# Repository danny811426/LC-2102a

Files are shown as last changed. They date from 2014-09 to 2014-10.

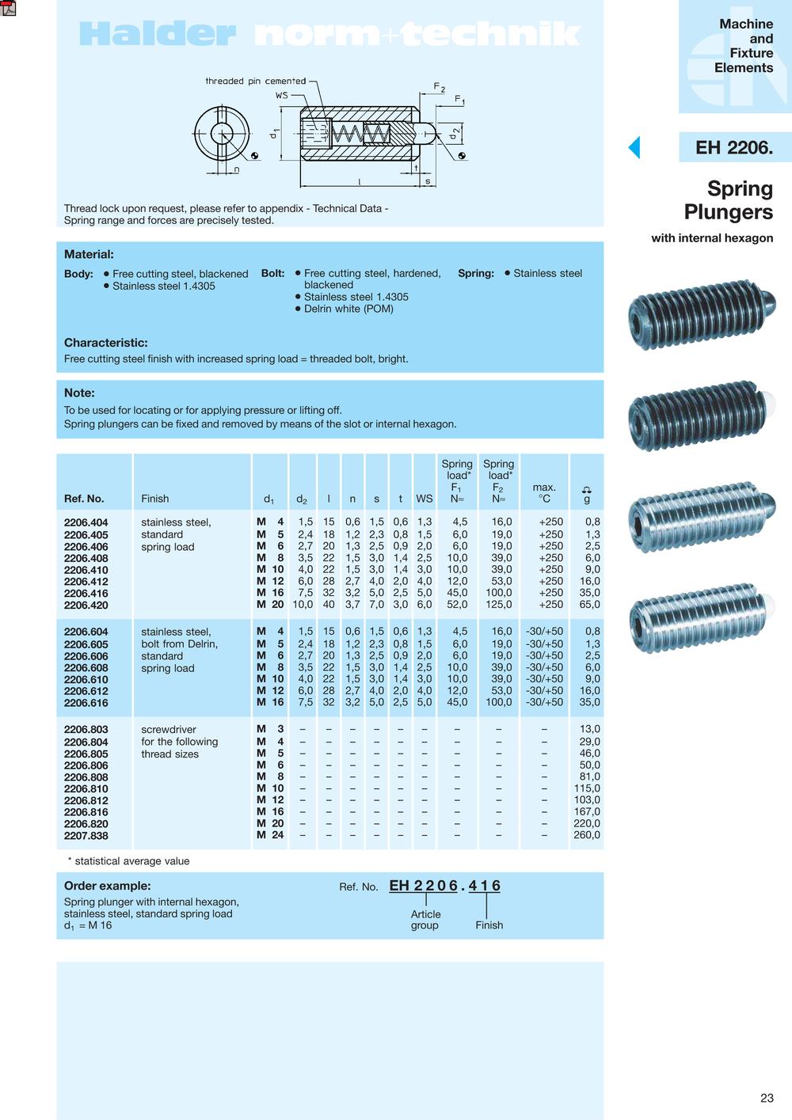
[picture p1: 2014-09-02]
design/datasheets/2206.404 spring plungers.jpg

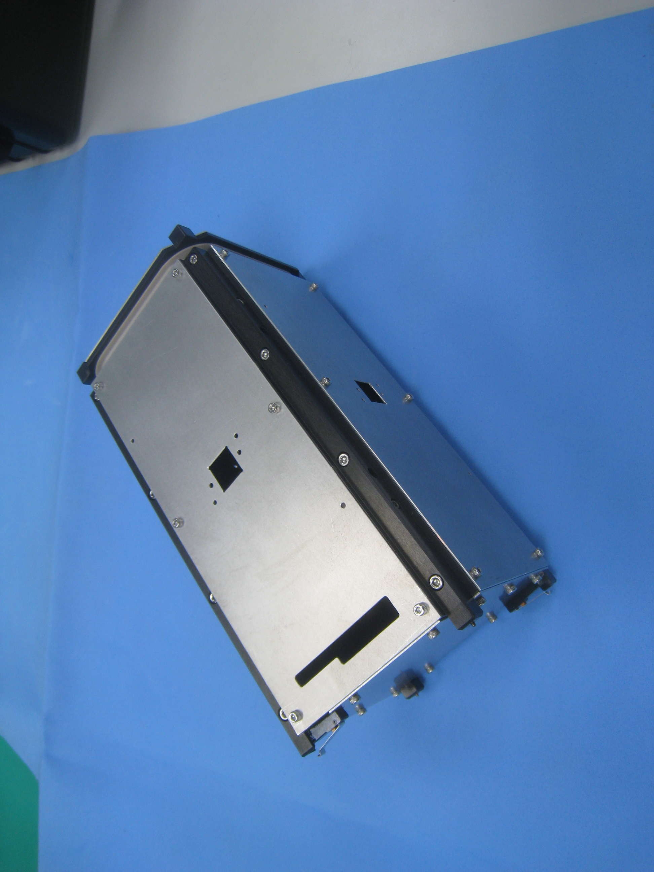
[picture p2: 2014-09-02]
documentation/pictures/IMG_3512.JPG

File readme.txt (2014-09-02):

---------------------------------------
LibreCube LC-2102a 2U CubeSat Structure 
---------------------------------------

OVERVIEW
--------
The LC-2102a 2U CubeSat Structure is a rigid and modular structure for 
nanosatellites that fully conforms to the CubeSat specification. It consists 
of four anodized side frames and a bottom frame, an antenna mounting ring, 
and panels. The frame and panels are made of 6061 aluminium alloy, while the 
antenna mounting ring is made of PEEK. The product fits CubeSat-Kit compatible 
boards and standard PC104 boards.

DISCLAIMER
----------
This product package is distributed in the hope that it will be useful, but 
WITHOUT ANY WARRANTY; without even the implied warranty of MERCHANTABILITY or 
FITNESS FOR A PARTICULAR PURPOSE. See the applicable licenses for more details.

AUTHORS
-------
Release a
* Artur Scholz <artur.scholz@cubesat.de>
* Yannick Lammen

ACKNOWLEDGEMENTS
----------------
The original work (Release a) was carried out at and with support from 
National Cheng Kung University (www.ncku.edu.tw) under supervision of 
Prof. Jiun-Jih Miau and Prof. Jyh-Ching Juang and with the help from students 
of PACELAB and MECLAB of National Cheng Kung University.

RELEASE HISTORY
---------------
Release a
* First release

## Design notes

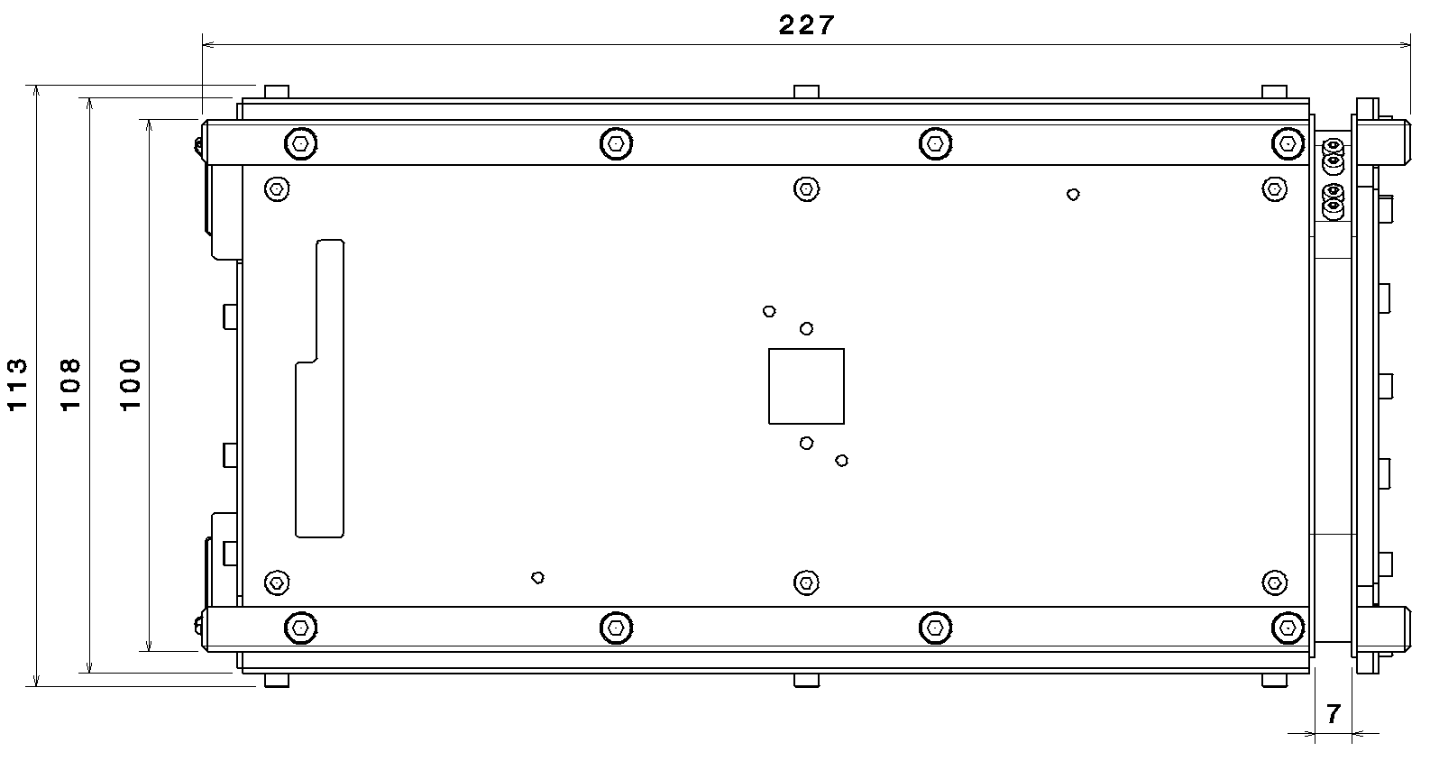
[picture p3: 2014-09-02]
documentation/figures/dimensions.tif

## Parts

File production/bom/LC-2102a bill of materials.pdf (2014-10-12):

Sheet1

Page 1

LC-2102a Bill of Materials

Item | Description | Qty | Part Number / Notes
1 | frame A | 2 | Al-6061, anodized
2 | frame B | 2 | Al-6061, anodized
3 | frame C | 1 | Al-6061, anodized
4 | panel 1 | 1 | Al-6061
5 | panel 2 | 3 | Al-6061
6 | panel 5 | 1 | Al-6061
7 | panel 6 | 1 | Al-6061
8 | board mounting block FLU | 2 | PEEK
9 | board mounting block FRU | 2 | PEEK
10 | board mounting block BRU | 1 | PEEK
11 | board mounting block BLD | 1 | PEEK
12 | board mounting block BLU | 1 | PEEK
13 | board mounting block BRD | 1 | PEEK
14 | antenna ring | 1 | PEEK
15 | M2x10 | 10 | ISO 4762 hexagon socket head cap, aluminum
16 | M2.5x4 | 44 | ISO 4762 hexagon socket head cap, aluminum
17 | M2.5x5 | 16 | ISO 4762 hexagon socket head cap, aluminum
18 | M3x10 | 16 | ISO 4762 hexagon socket head cap, aluminum
19 | M3x16 | 10 | ISO 4762 hexagon socket head cap, aluminum
20 | separation spring | 2 | 15 mm body, 1.5 mm ball and ball height (IMAO: PL4-SUS; KIPP: 03055-04)
21 | deployment switch | 2 | (Digikey: SW247-ND; OMRON: SS-10GL13T)

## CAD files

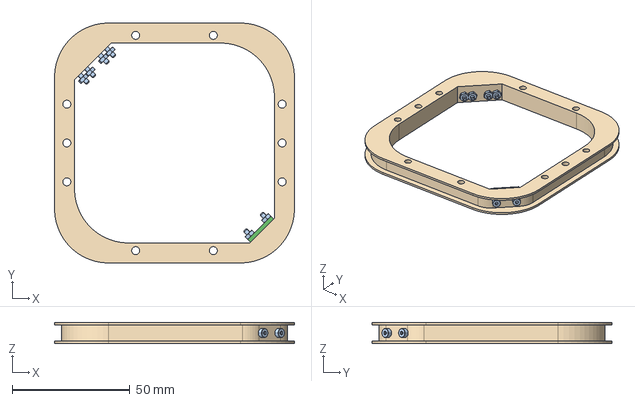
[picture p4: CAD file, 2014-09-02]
production/mechanical/iges/assemblies/antenna ring assembly.igs
102.0 x 102.0 x 9.00 mm

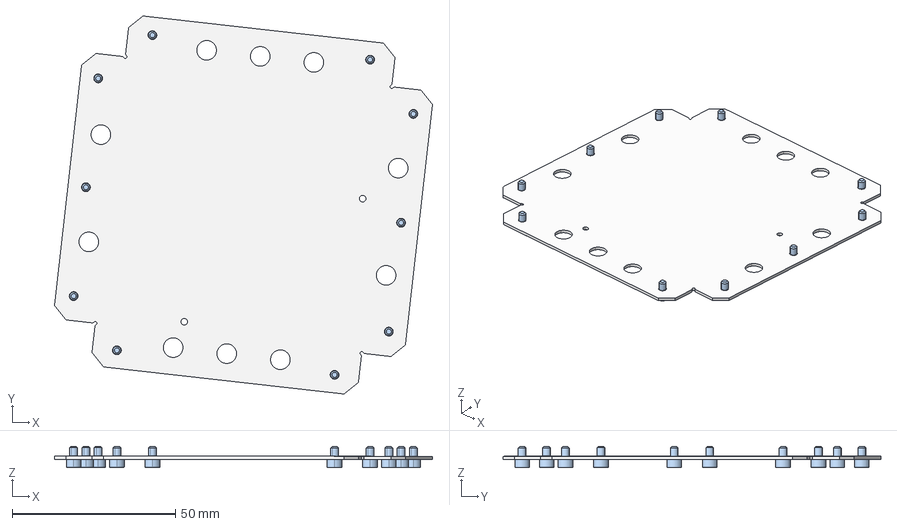
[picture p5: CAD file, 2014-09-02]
production/mechanical/iges/assemblies/bottom panel assembly.igs
115.6 x 115.6 x 6.56 mm

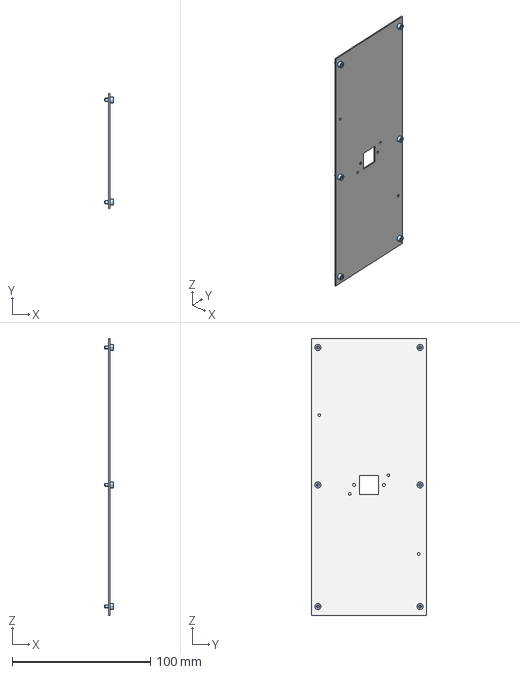
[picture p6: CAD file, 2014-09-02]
production/mechanical/iges/assemblies/left panel assembly.igs
6.50 x 83.0 x 200.5 mm

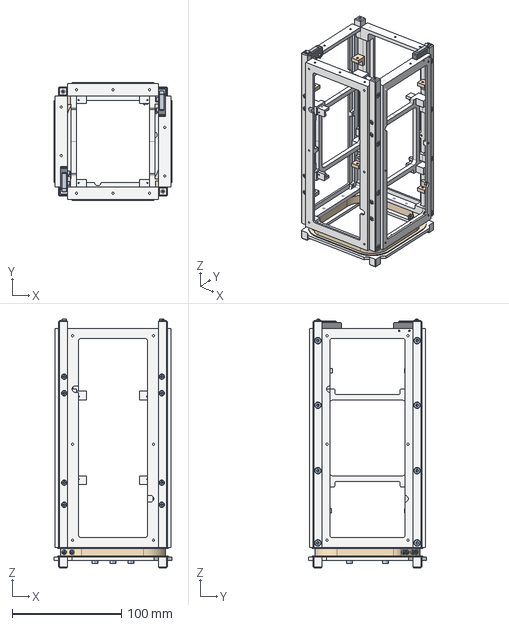
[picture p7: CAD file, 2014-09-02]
production/mechanical/iges/assemblies/structure assembly.igs
108.0 x 108.0 x 228.3 mm

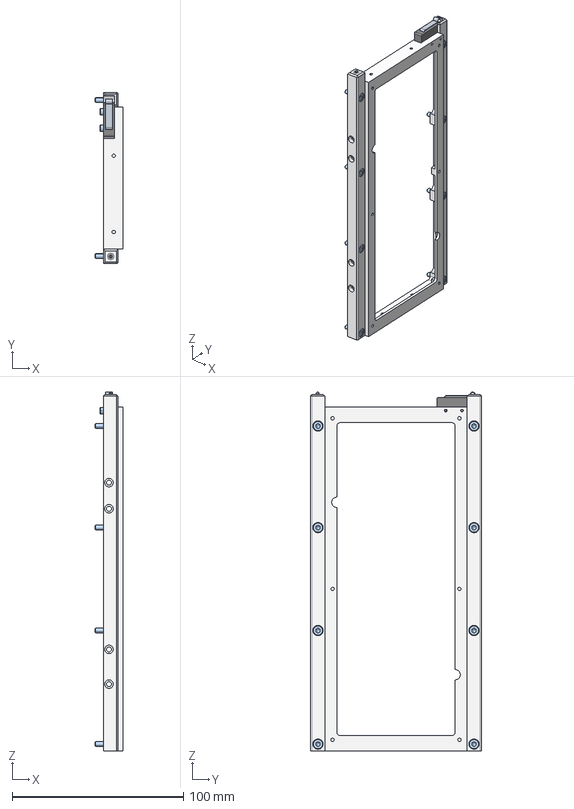
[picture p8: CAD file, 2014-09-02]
production/mechanical/iges/assemblies/frame a assembly.igs
16.5 x 100.0 x 209.3 mm

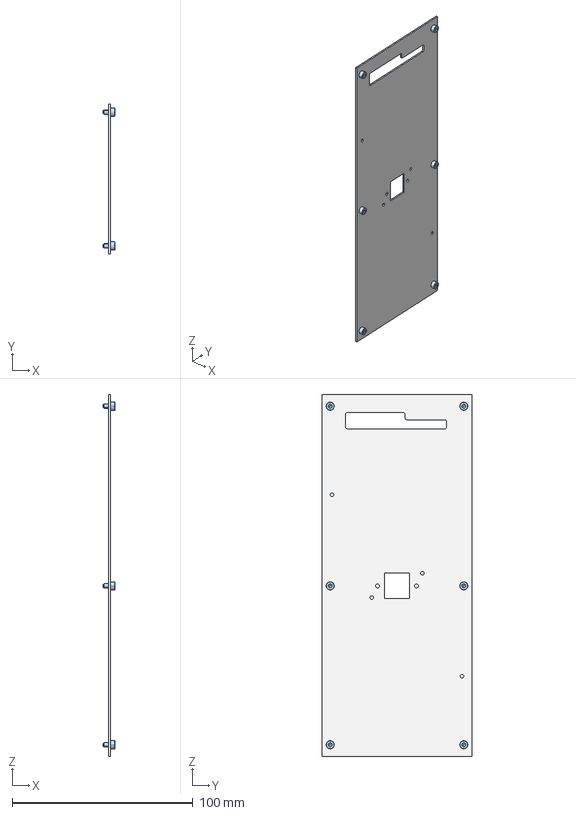
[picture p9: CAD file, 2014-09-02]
production/mechanical/iges/assemblies/front panel assembly.igs
6.50 x 83.0 x 200.5 mm

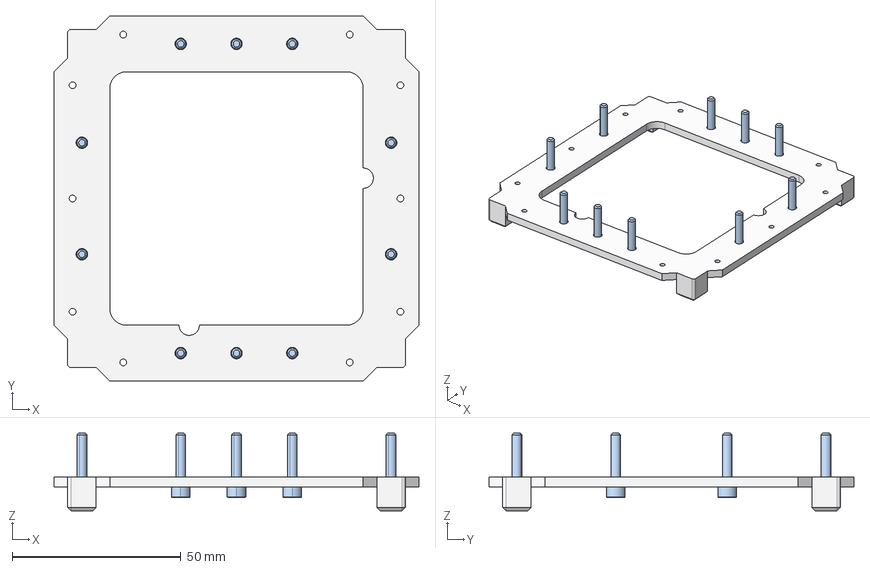
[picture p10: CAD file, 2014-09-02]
production/mechanical/iges/assemblies/frame c assembly.igs
108.0 x 108.0 x 23.0 mm

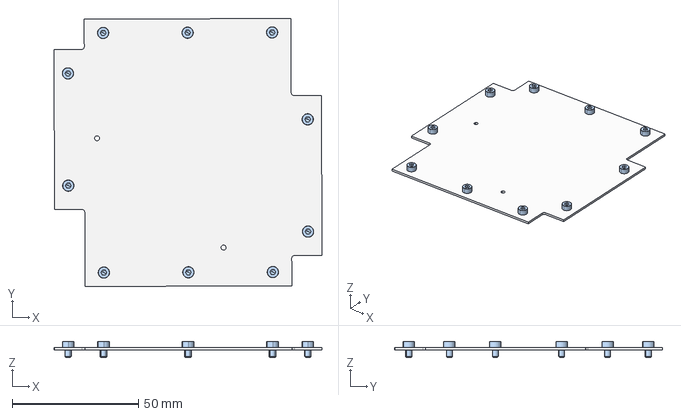
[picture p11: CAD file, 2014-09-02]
production/mechanical/iges/assemblies/top panel assembly.igs
106.3 x 106.3 x 6.50 mm

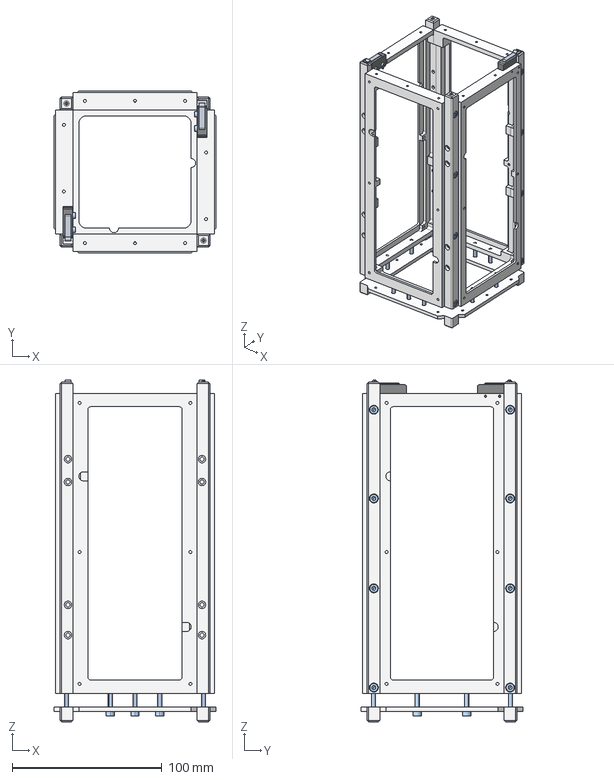
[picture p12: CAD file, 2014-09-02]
production/mechanical/iges/assemblies/frame assembly.igs
108.0 x 108.0 x 228.3 mm

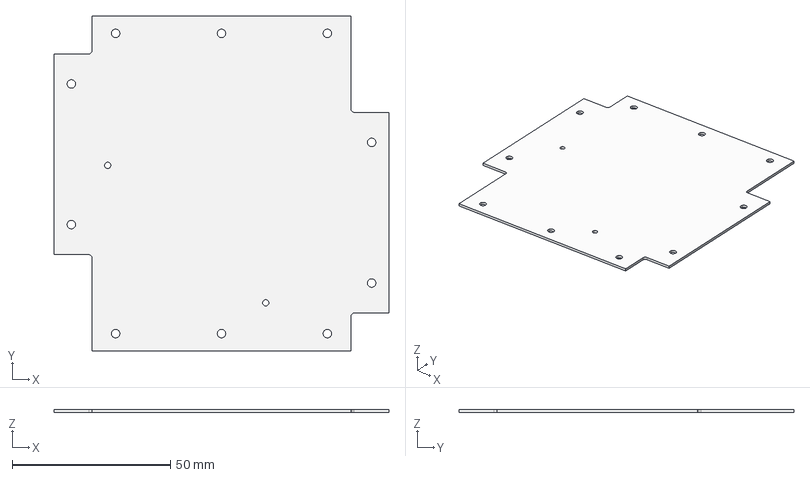
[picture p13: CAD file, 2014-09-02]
production/mechanical/iges/parts/panel 5.igs
106.0 x 106.0 x 1.00 mm

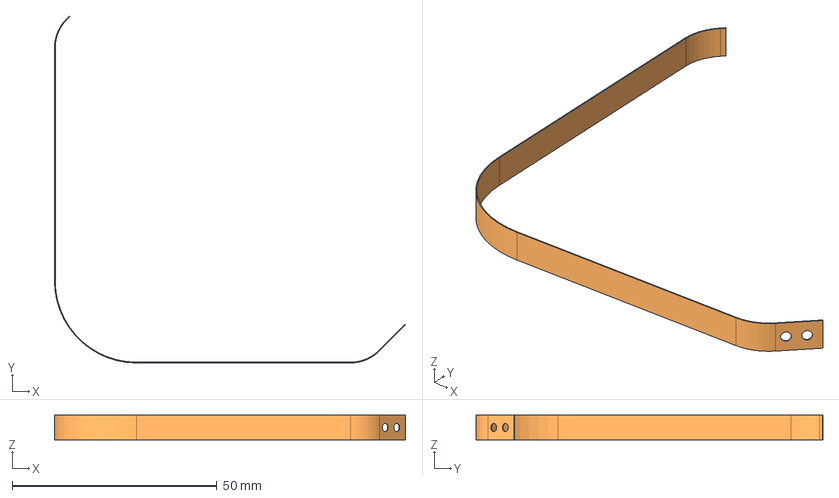
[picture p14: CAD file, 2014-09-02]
production/mechanical/iges/parts/dipole antenna folded.igs
85.6 x 84.6 x 6.00 mm

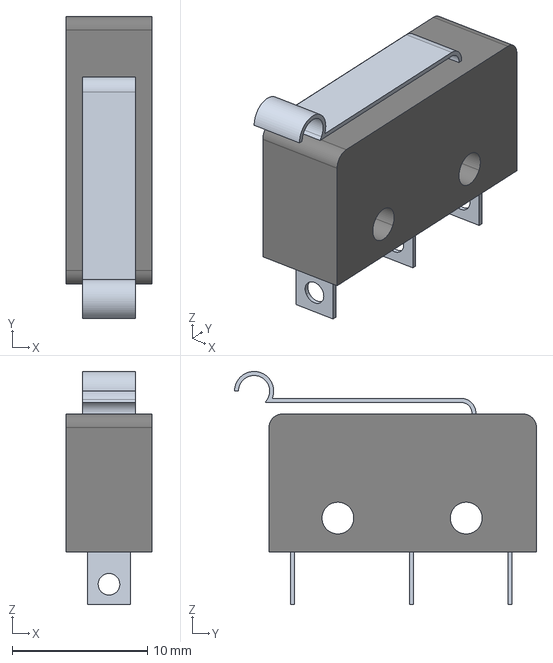
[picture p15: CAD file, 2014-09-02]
production/mechanical/iges/parts/deployment switch.igs
6.40 x 22.4 x 17.2 mm

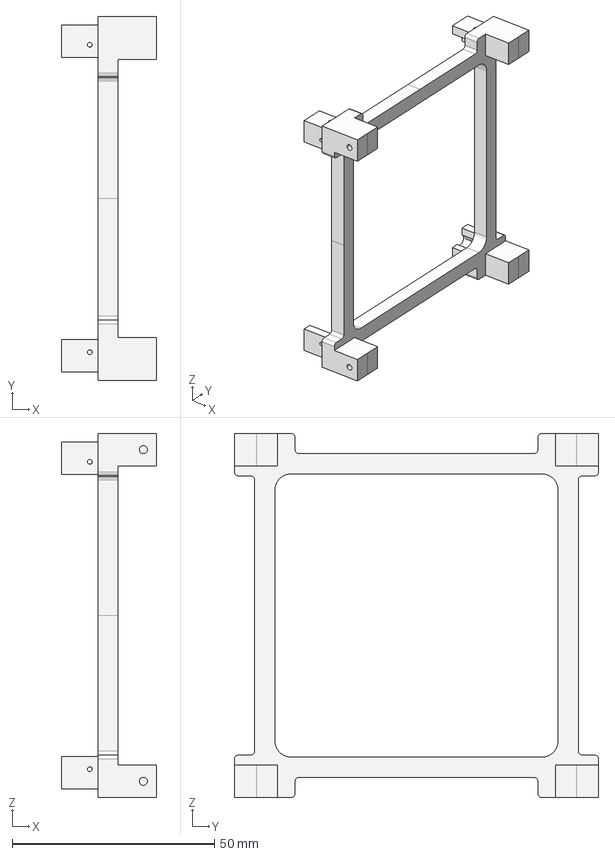
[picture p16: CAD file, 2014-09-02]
production/mechanical/iges/parts/frame d.igs
23.5 x 90.0 x 90.0 mm

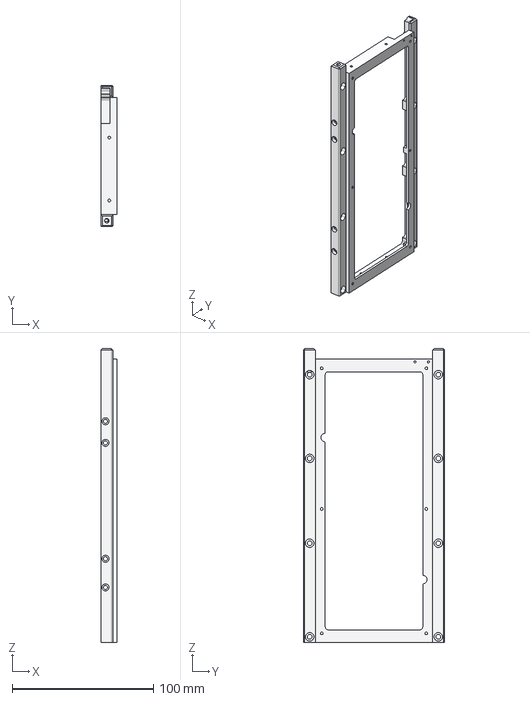
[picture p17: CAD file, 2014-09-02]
production/mechanical/iges/parts/frame a.igs
11.5 x 100.0 x 208.0 mm

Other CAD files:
production/mechanical/iges/assemblies/back panel assembly.igs
production/mechanical/iges/assemblies/right panel assembly.igs
production/mechanical/iges/parts/separation spring.igs
production/mechanical/iges/parts/board mounting block fru.igs
design/mechanical/assembly.CATProduct
design/mechanical/screws/ISO_4762_M2.5x4_STEEL_HEXAGON_SOCKET_HEAD_CAP_SCREW.CATPart
design/mechanical/screws/ISO_4762_M2.5x5_STEEL_HEXAGON_SOCKET_HEAD_CAP_SCREW.CATPart
design/mechanical/screws/ISO_4762_M2x10_STEEL_HEXAGON_SOCKET_HEAD_CAP_SCREW.CATPart
design/mechanical/screws/ISO_4762_M3x10_STEEL_HEXAGON_SOCKET_HEAD_CAP_SCREW.CATPart
design/mechanical/screws/ISO_4762_M3x16_STEEL_HEXAGON_SOCKET_HEAD_CAP_SCREW.CATPart
design/mechanical/side panels/back panel assembly.CATProduct
design/mechanical/side panels/bottom panel assembly.CATProduct
design/mechanical/side panels/front panel assembly.CATProduct
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

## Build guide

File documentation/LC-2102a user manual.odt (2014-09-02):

LC2102a

2U CubeSat Structure

Document change log

Rev. | Date | Author | Pages | Description
0 | 2014-07-12 | Artur Scholz | All | Initial release

# Introduction

The LC-2102a 2U CubeSat Structure is a rigid and modular structure for nanosatellites that fully conforms to the CubeSat specification. It consists of four anodized side frames and a bottom frame, an antenna mounting ring, and panels. The frame and panels are made of 6061 aluminium alloy, while the antenna mounting ring is made of PEEK. The product fits CubeSat-Kit compatible boards and standard PC104 boards. It is easily assembled with 46 screws (plus 44 panel screws).

Illustration 1 is an exploded view of the product with two panels removed. It shows the annotation for the main components of the product. The coordinate systems shown are the CubeSat reference frame and the reference frame for handling and assembly.

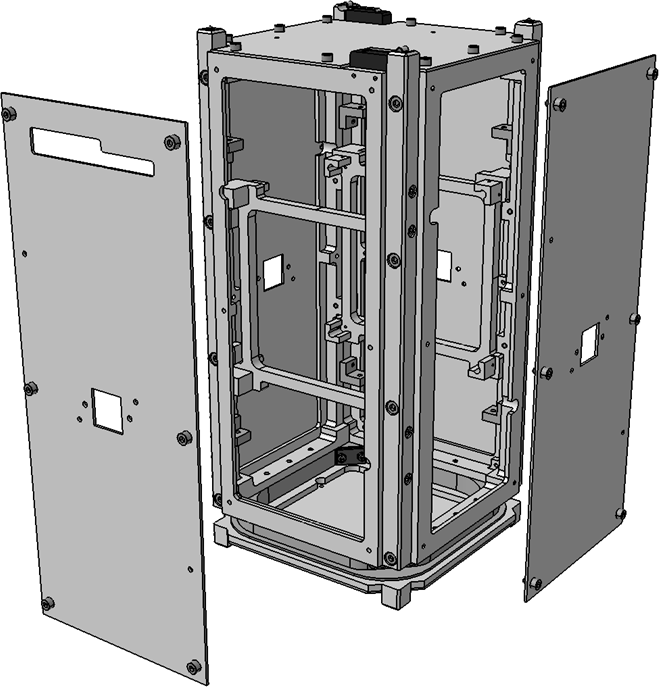
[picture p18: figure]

Illustration 1: Exploded view of product

Up

Front

Right

+XCRF

+YCRF

+ZCRF

Top panel (-Z)

Frame A

Frame B

Rail

Right panel (+Y)

Antenna ring

Deployment switch

Separation spring

Access port opening

Front panel (-X)

Secondary frame

Sun sensor opening

Board mounting block

Frame C

Features:

- Rigid 2 mm 6061 aluminium frame and 1mm 6061 aluminium panels
- Modular design
- Easy to assemble and integrate
- Redundant separation springs and redundant deployment switches
- Antenna mounting ring
- For CubeSat-Kit compatible boards and PC104 boards
- Total mass: 704 grams
- Qualified for PSLV, DNEPR and other launch rockets
- First natural frequency > 400 Hz

# Applicable and reference documents

Reference | Title | Issue
AD1 | CubeSat Design Specification | 12 or later

Reference | Title | Issue
RD1 | CubeSat Board Specification

# Definitions and abbreviations

Term | Definition
Assembly | The process of mating parts to obtain a low level configuration
Integration | The process of physically and functionally combining lower level products to obtain a particular functional configuration
Fixing | The permanent locking of fasteners
Mounting | Mating of parts using fasteners

Abbreviation | Definition
CRF | CubeSat reference frame
ESD | Electrostatic discharge
RBF | Remove-before-flight
SMS | Structure and mechanisms system

# Specification

## Absolute maximum ratings

Parameter | Min | Max | Unit
Current through deployment switch | | 10 | A

| Exceeding the limits specified in the table above may result in permanent damage to the device and harm to products and personal.

## Physical characteristics

Parameter | Min | Nom | Max | Unit
Total mass | | 704 | | g
First natural frequency | 400 | | | Hz
Centre of gravity, Gx | | 0.11 | | mm
Centre of gravity, Gy | | 0 | | mm
Centre of gravity, Gz | | 4.67 | | mm
Moment of inertia, Ixx | | 6.00E-003 | | kg*m**2
Moment of inertia, Iyy | | 5.00E-003 | | kg*m**2
Moment of inertia, Izz | | 3.00E-003 | | kg*m**2
Moment of inertia, off-diagonal | | | 1.00E-005 | kg*m**2

* All values are given with respect to the CubeSat reference frame, with its origin in the geometric centre of the CubeSat

## Other characteristics

### Technology readiness level

The product in its configuration has TRL 8 and is qualified for space operation. It has been qualified against typical launch loads and low earth space environment.

### Compatibility

The product is in full conformance with the CubeSat Design Specification. It can integrate boards that conform to the CubeSat Board Specification form factor and other custom-made boards.

# Interfaces

## Mechanical interfaces

### External interfaces

The product has interfaces to the deployer during launch and it has interfaces to mechanical ground support equipment during assembly and testing. The external dimensions of the product are shown in Illustration 2. Also shown are the dimensions of the access port opening. These, and any other side panel openings (such as for the sun sensor) are fully customizable. The side panels allow for mounting of components such as sensors and solar panels.

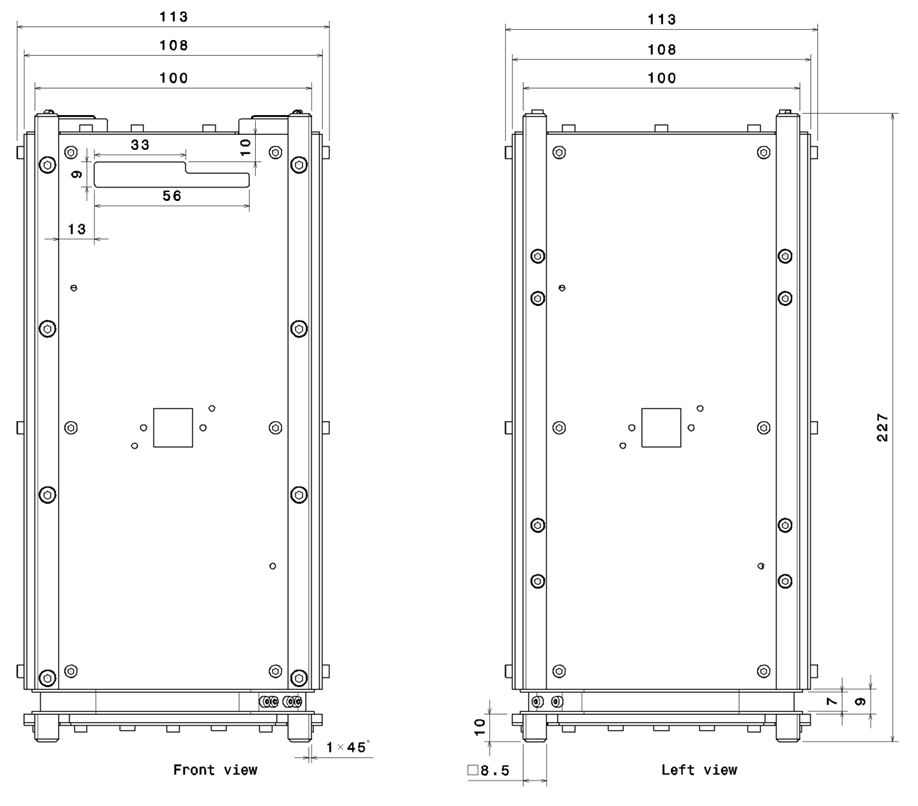
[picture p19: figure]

Illustration 2: External dimensions

### Internal interfaces

The product interfaces to the interior satellite components through its main structure. The structure provides through-holes for M2.5 screws at each frame A as shown in Illustration 3. These can be used to either mount components (such as payload) directly onto the frame, or by using mounting blocks for the boards as shown in Illustration 4.

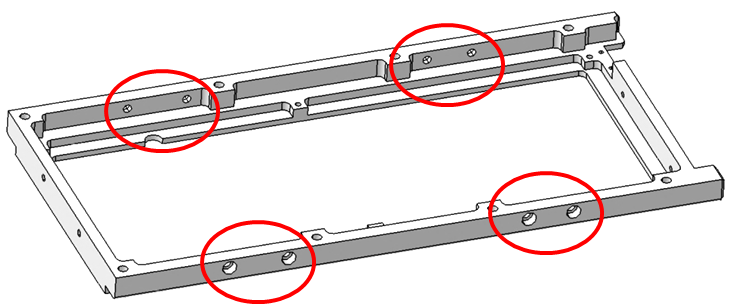
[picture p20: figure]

Illustration 3: Mounting holes

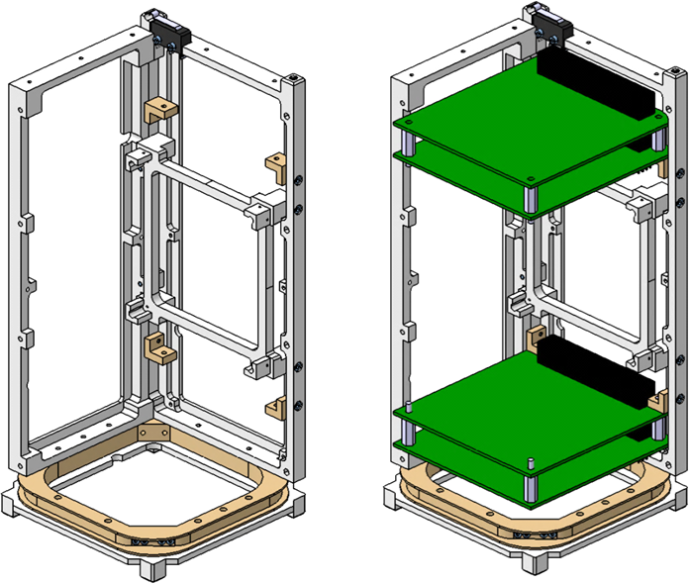
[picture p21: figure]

Illustration 4: Example of a mounting configuration for interior components

Up

Front Right

The interior boards should conform to the board shape as specified in the CubeSat Board Specification and shown in Illustration 5.

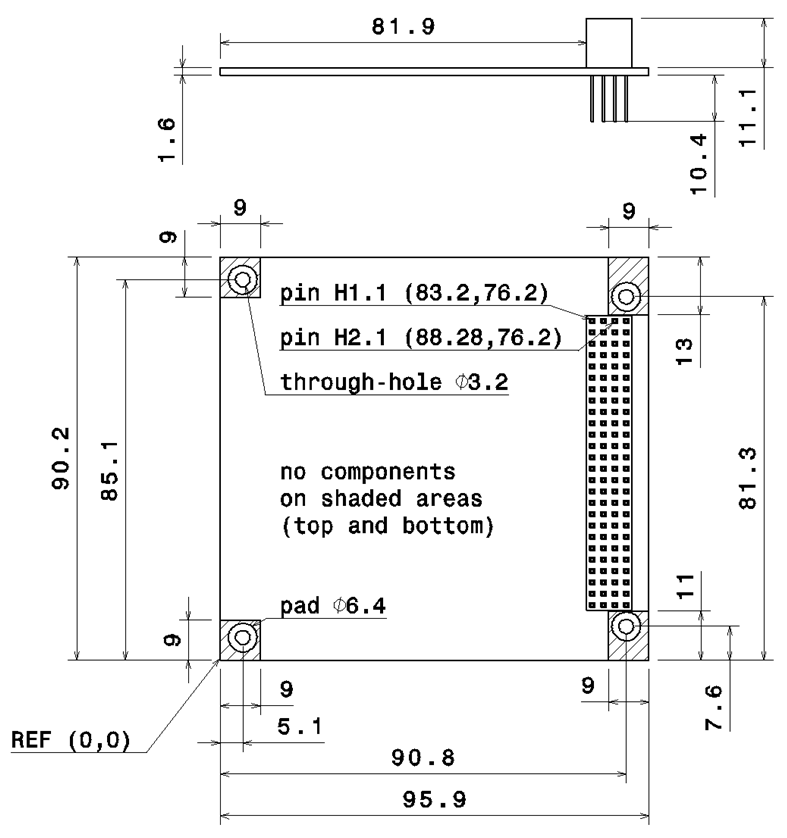
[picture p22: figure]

Illustration 5: Recommended shape of interior boards

## Electrical interfaces

The only electrical interfaces of the product are the deployment switches. The functioning of the switch is shown in Illustration 6. Depending on the deployment switch circuit logic of the satellite, not all of the terminals may be used and can be removed.

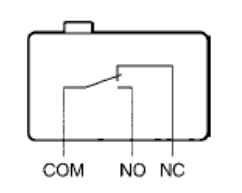
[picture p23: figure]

Illustration 6: Deployment switch diagram

# Design description

## Main structure

The main structure was designed not for optimized (low) weight, but for rigidity and modularity. All screws are easily accessible and the structure can be assembled and disassembled quickly.

## Side panels

The side panels can be customized to fit sensors and solar panels. The current design allows for mounting of attitude sensors and/or cameras in the centre. It also provides an access window to the hosted subsystem boards on the front panel.

## Deployment switches and separation springs

Separation springs are integrated on the top end of two opposite rails. On the two remaining rails, the deployment switches are mounted on top. This mechanism combines robustness with simplicity.

## Antenna ring and deployment

The antenna ring provides for mounting an UHF dipole antenna. The antenna is stored during launch and released upon orbit injection. This is usually done via melting a nylon string that holds the free ends of the dipoles together. The mechanisms requires an external system to provide the power for this mechanism.

# Handling and storage

Be careful when handling the product and observe cleanliness requirements. To clean the product, use a lightly moist tissue.

| Use gloves when handling the product and ensure cleanliness at all times.

| Be careful in particular not to break the deployment switch levers.

Store the product in a clean and dry environment at room temperature. The product may be stored in assembled or disassembled configuration.

2U CubeSat Structure Ref : LC-2102a-MAN-001 Issue : 1 Rev. : 0 Date : 2014-07-12 Page : 11

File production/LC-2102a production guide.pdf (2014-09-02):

2U CubeSat Structure

Ref | : LC-2102a-MAN-002
Issue | : 1 | Rev. | : 0
Date | : 2014-07-11
Production Guide | Page | : 1

# LC-2102a 2U CubeSat Structure Production Guide

Document change log
Rev. | Date | Author | Pages | Description
0 | 2014-07-11 | Artur Scholz | All | Initial release

2U CubeSat Structure

Production Guide | Page : 2
Issue | : 1 | Rev. | : 0
Date | : 2014-07-11

## Table of Contents

2U CubeSat Structure

Production Guide | Page : 3
Issue | : 1 | Rev. | : 0
Date | : 2014-07-11

## 1 Introduction

This document provides the necessary information for production and assembly of the product as shown in Illustration 1

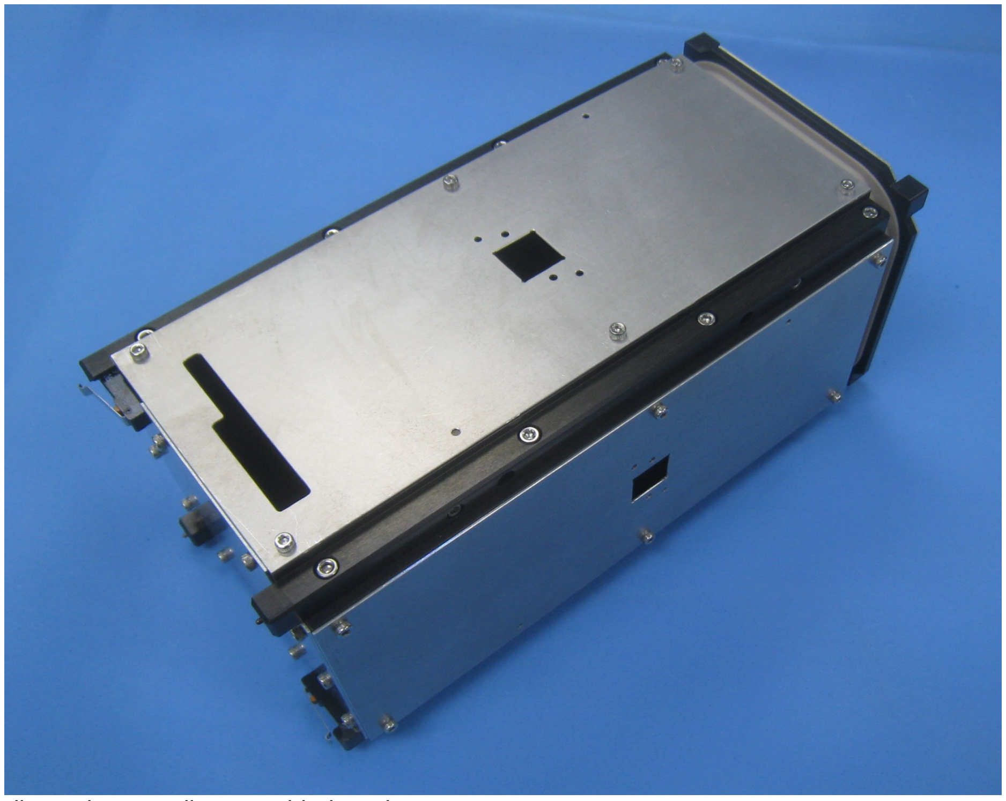
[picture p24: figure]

Illustration 1: Fully assembled product

## 2 Hardware

### 2.1 Hardware preparation

The product consists of mechanical parts, screws, a few other components, and a PCB for the antenna deployment mechanisms.

Structural parts and the PCB must be manufactured, using the information provided in the product package. Screws and the components can be bought off the shelf.

2U CubeSat Structure

Production Guide | Page : 4
Issue | : 1 | Rev. | : 0
Date | : 2014-07-11

### 2.2 Assembly overview

Prepare a clean, bright, spacious and flat work desk for the assembly. When doing the flight integration of other satellite parts (in particular the electronic systems) ensure ESD protection and adherence to cleanliness requirements. Prepare all parts, screws, tools and put in convenient reach.

Do not use excessive force when mounting the screws. Recommended values for bolt torque (according to VDI 2230) are shown in Table 1.

Table 1: Recommended bolt torques
Thread | M2 | M2.5 | M3
Bolt torque [Nm] | 0.36 | 0.73 | 1.3

### 2.2.1 Parts

2x | Frame A
2x | Frame B
1x | Frame C
1x | Antenna Ring
1x | Front Panel (Panel 1)
3x | Side Panel (Panel 2)
1x | Top Panel (Panel 5)
1x | Bottom Panel (Panel 6)
8x | Mounting Blocks (2x FLU, 2x FRU, 1x BRU, 1x BLU, 1x BRD, 1x BLD)
2x | Separation Springs
2x | Deployment Switches

### 2.2.2 Screws

4x | M2x10 | Hexagon socket head screw
16x M2.5x5 | Hexagon socket head screw
16x M3x10 | Hexagon socket head screw
10x M3x16 | Hexagon socket head screw
44x M2.5x4 | Hexagon socket head screw

### 2.2.3 Tools

Hex key screwdriver 1.5 mm | for M2 hex socket screws
Hex key screwdriver 2 mm | for M2.5 hex socket screws
Hex key screwdriver 2.5 mm | for M3 hex socket screws

2U CubeSat Structure

Production Guide | Page : 5
Issue | : 1 | Rev. | : 0
Date | : 2014-07-11

### 2.3 Component assembly

The following sections describe the preparations that shall be carried out before the stand-alone integration.

### 2.3.1 Assembly of Frame A

The preparation of each Frame A is identical. See Illustration 2 and Illustration 3 for details.

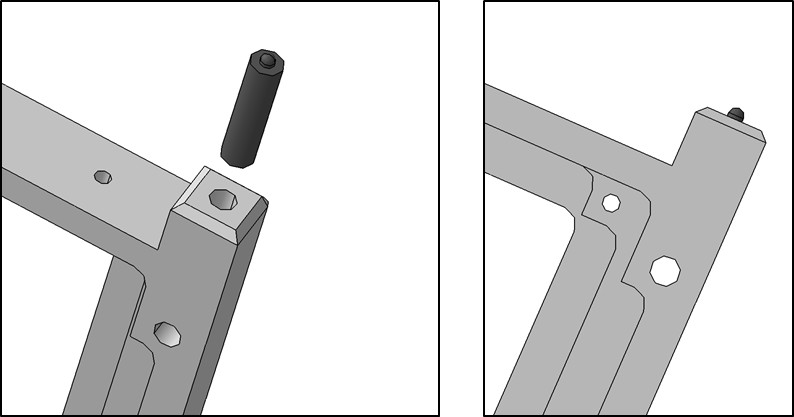
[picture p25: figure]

It is recommended to apply screw lock (such as Loctite) to permanently fix the Separation Spring onto the frame.

Illustration 2: Screw the Separation Spring into the frame until only the tip shows out

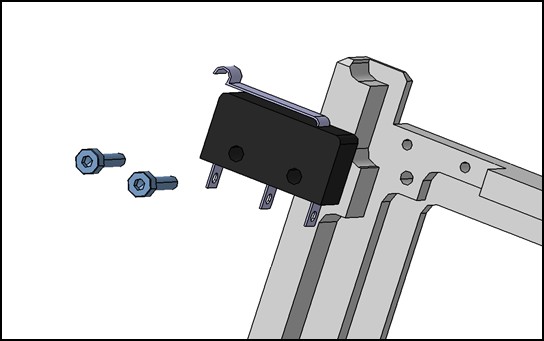
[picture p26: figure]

Illustration 3: Screw the Deployment Switch to the frame with 2x M2x10 screws

2U CubeSat Structure

Production Guide | Page : 6
Issue | : 1 | Rev. | : 0
Date | : 2014-07-11

### 2.4 Product assembly

Ensure that each Frame A has been prepared according to the instructions given in the previous section. Although both are identical, one shall be declared as the front frame (in -X direction). (Later during the integration this front frame will be equipped with the front panel.)

Take the Frame A that is designated as the front frame. Mount Frame B to Frame A with 4x M3x10 screws (Illustration 4). Do not fasten the screws tightly and allow for some play. Mount the other Frame B to Frame A with 4x M3x10 screws. Again, do not fasten the screws tightly and allow for some play.

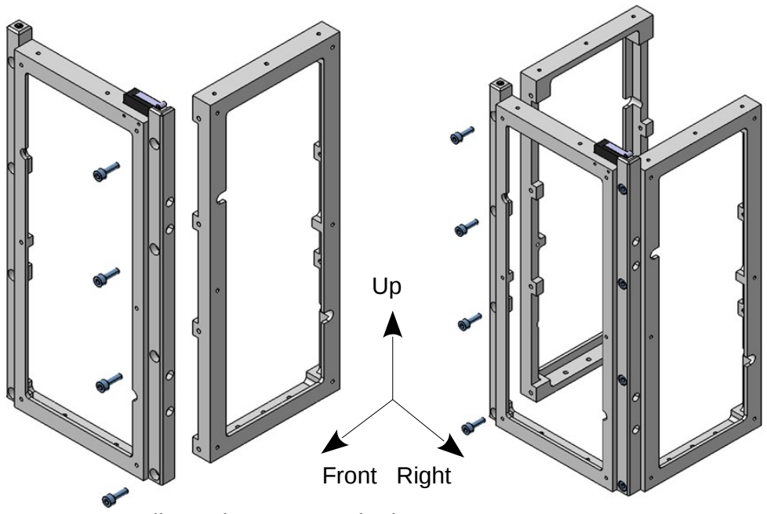
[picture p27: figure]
Front Right

Mount the other Frame A to the assembly with 8x M3x10 screws (Illustration 5). Do not fasten the screws tightly and allow for some play.

Erect the assembly on a flat surface in upright position, ensure that the frame is aligned correctly, and fasten all screws. When tightening the screws proceed in a cross-wise fashion and start from inside and then mount outside screws (Illustration 6).

Illustration 4: Mount both Frame B to Frame A

2U CubeSat Structure

Production Guide | Page : 7
Issue | : 1 | Rev. | : 0
Date | : 2014-07-11

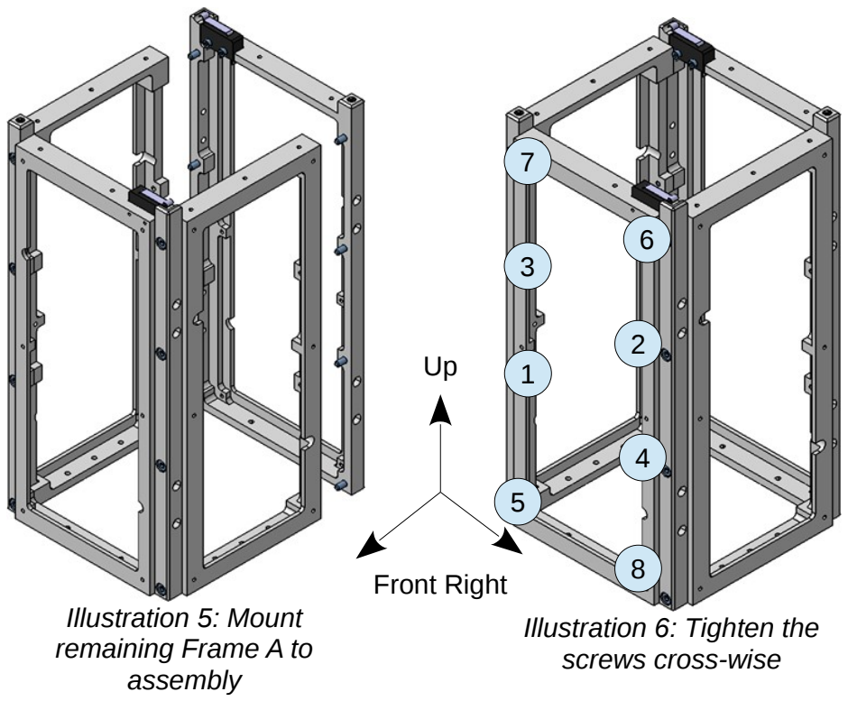
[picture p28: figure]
Illustration 5: Mount remaining Frame A to assembly; Illustration 6: Tighten the screws cross-wise; Front Right

Mount Antenna Ring and Frame C loosely onto the assembly using 10x M3x16 screws (Illustration 7). Align all rail surfaces and fix screws cross-wise (Illustration 8).

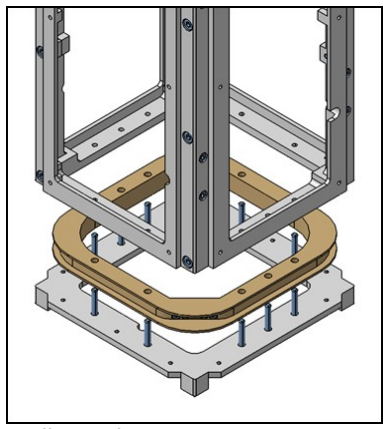
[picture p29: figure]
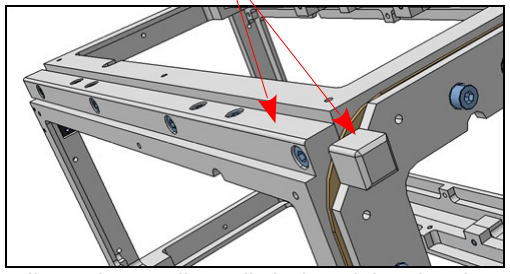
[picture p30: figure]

With the frame being assembled, the mounting blocks can now be installed. These blocks are used for mounting the internal boards during the satellite integration.

Illustration 7: Mount Antenna
Ring and Frame C to assembly

Illustration 8: Align rails before tightening the screws

Align all surfaces

2U CubeSat Structure

Production Guide | Page : 8
Issue | : 1 | Rev. | : 0
Date | : 2014-07-11

Each mounting block is installed with an M2.5x5 screw. The naming of the blocks corresponds to their position within the frame and is according to the following convention: [F(ront)/B(ack)][R(ight)/L(eft)][U(p)/D(own)].

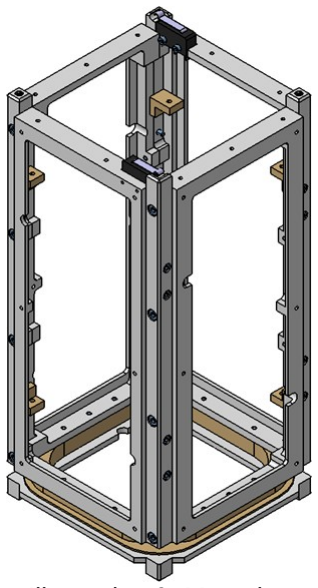
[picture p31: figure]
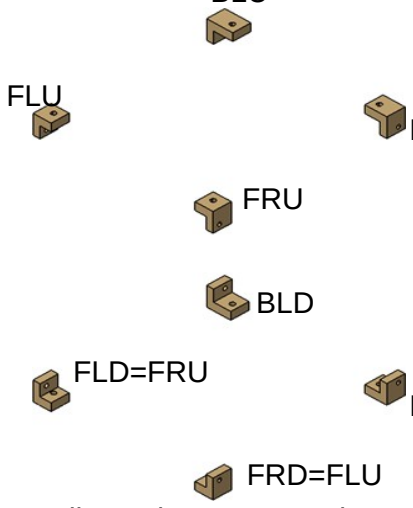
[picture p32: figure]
FLU; FRU; BLD; FLD=FRU; FRD=FLU

Then mount the Top Panel (Panel 5) with 10x M2.5x4 screws (Illustration 12). Mount Bottom Panel (Panel 6) with 10x M2.5x4 screws (Illustration 11). When mounting, observe the orientation of the panel to match the openings (as used for the solar cell harness).

Illustration 10: Mounting
blocks

BLU

BRU

BRD

Illustration 9: Mounting
blocks on place

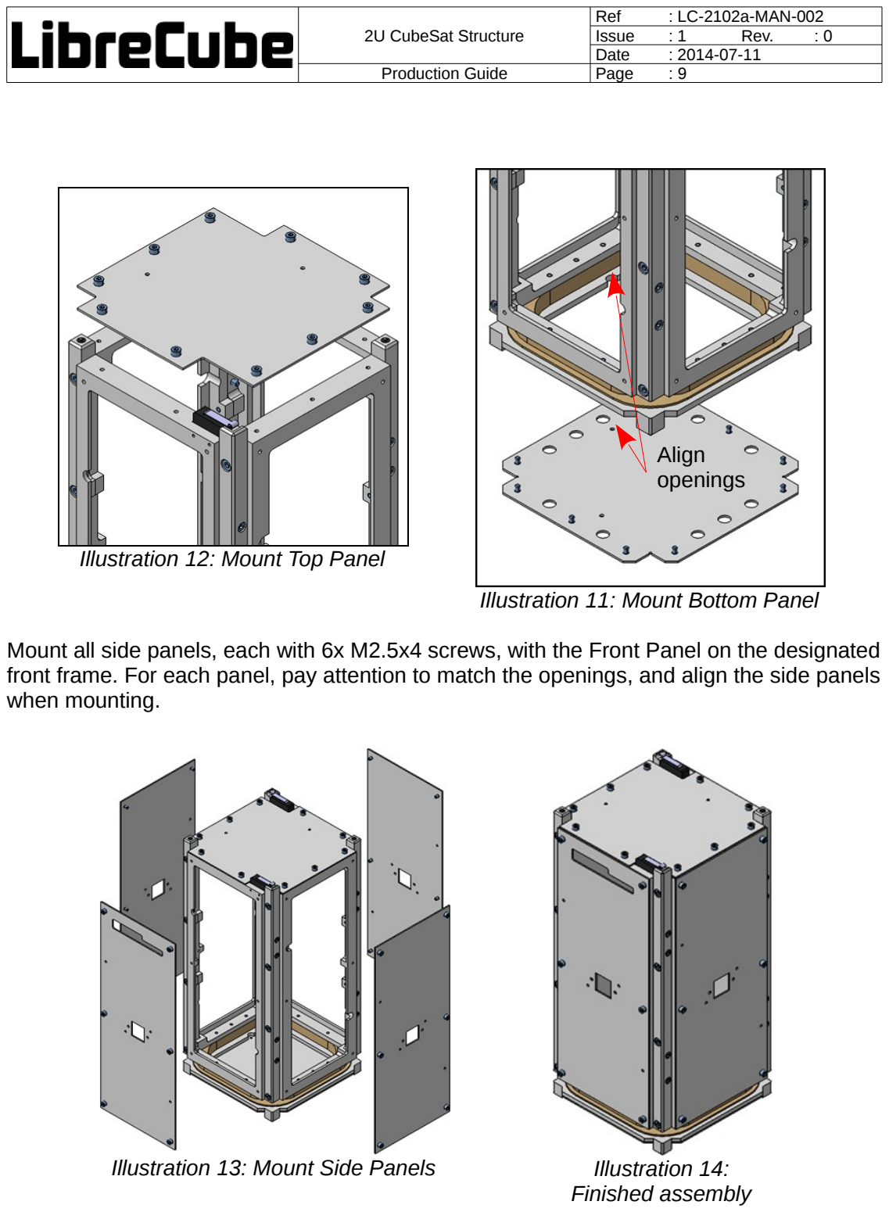
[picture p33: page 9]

2U CubeSat Structure

Production Guide | Page : 9
Issue | : 1 | Rev. | : 0
Date | : 2014-07-11

Mount all side panels, each with 6x M2.5x4 screws, with the Front Panel on the designated front frame. For each panel, pay attention to match the openings, and align the side panels when mounting.

Illustration 11: Mount Bottom Panel

Align
openings

Illustration 12: Mount Top Panel

Illustration 13: Mount Side Panels | Illustration 14: Finished assembly

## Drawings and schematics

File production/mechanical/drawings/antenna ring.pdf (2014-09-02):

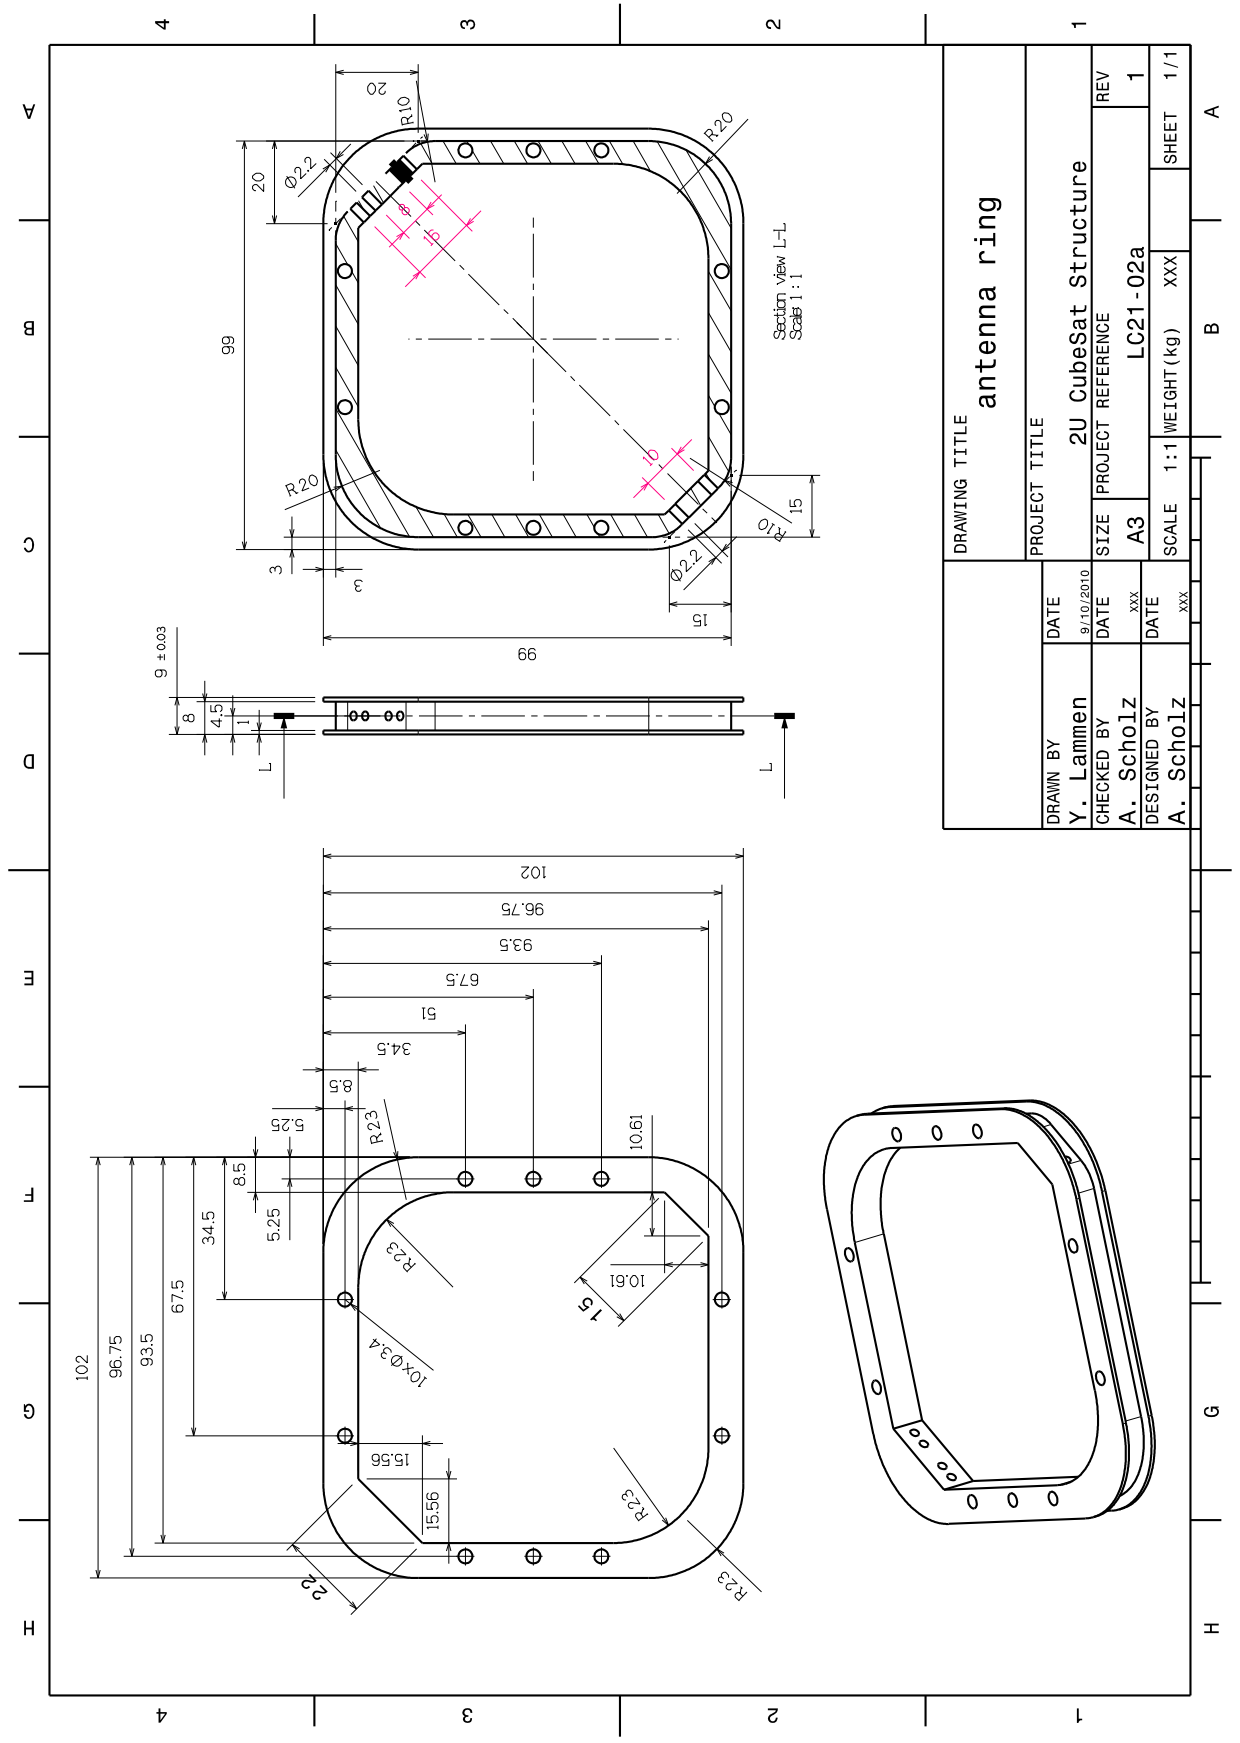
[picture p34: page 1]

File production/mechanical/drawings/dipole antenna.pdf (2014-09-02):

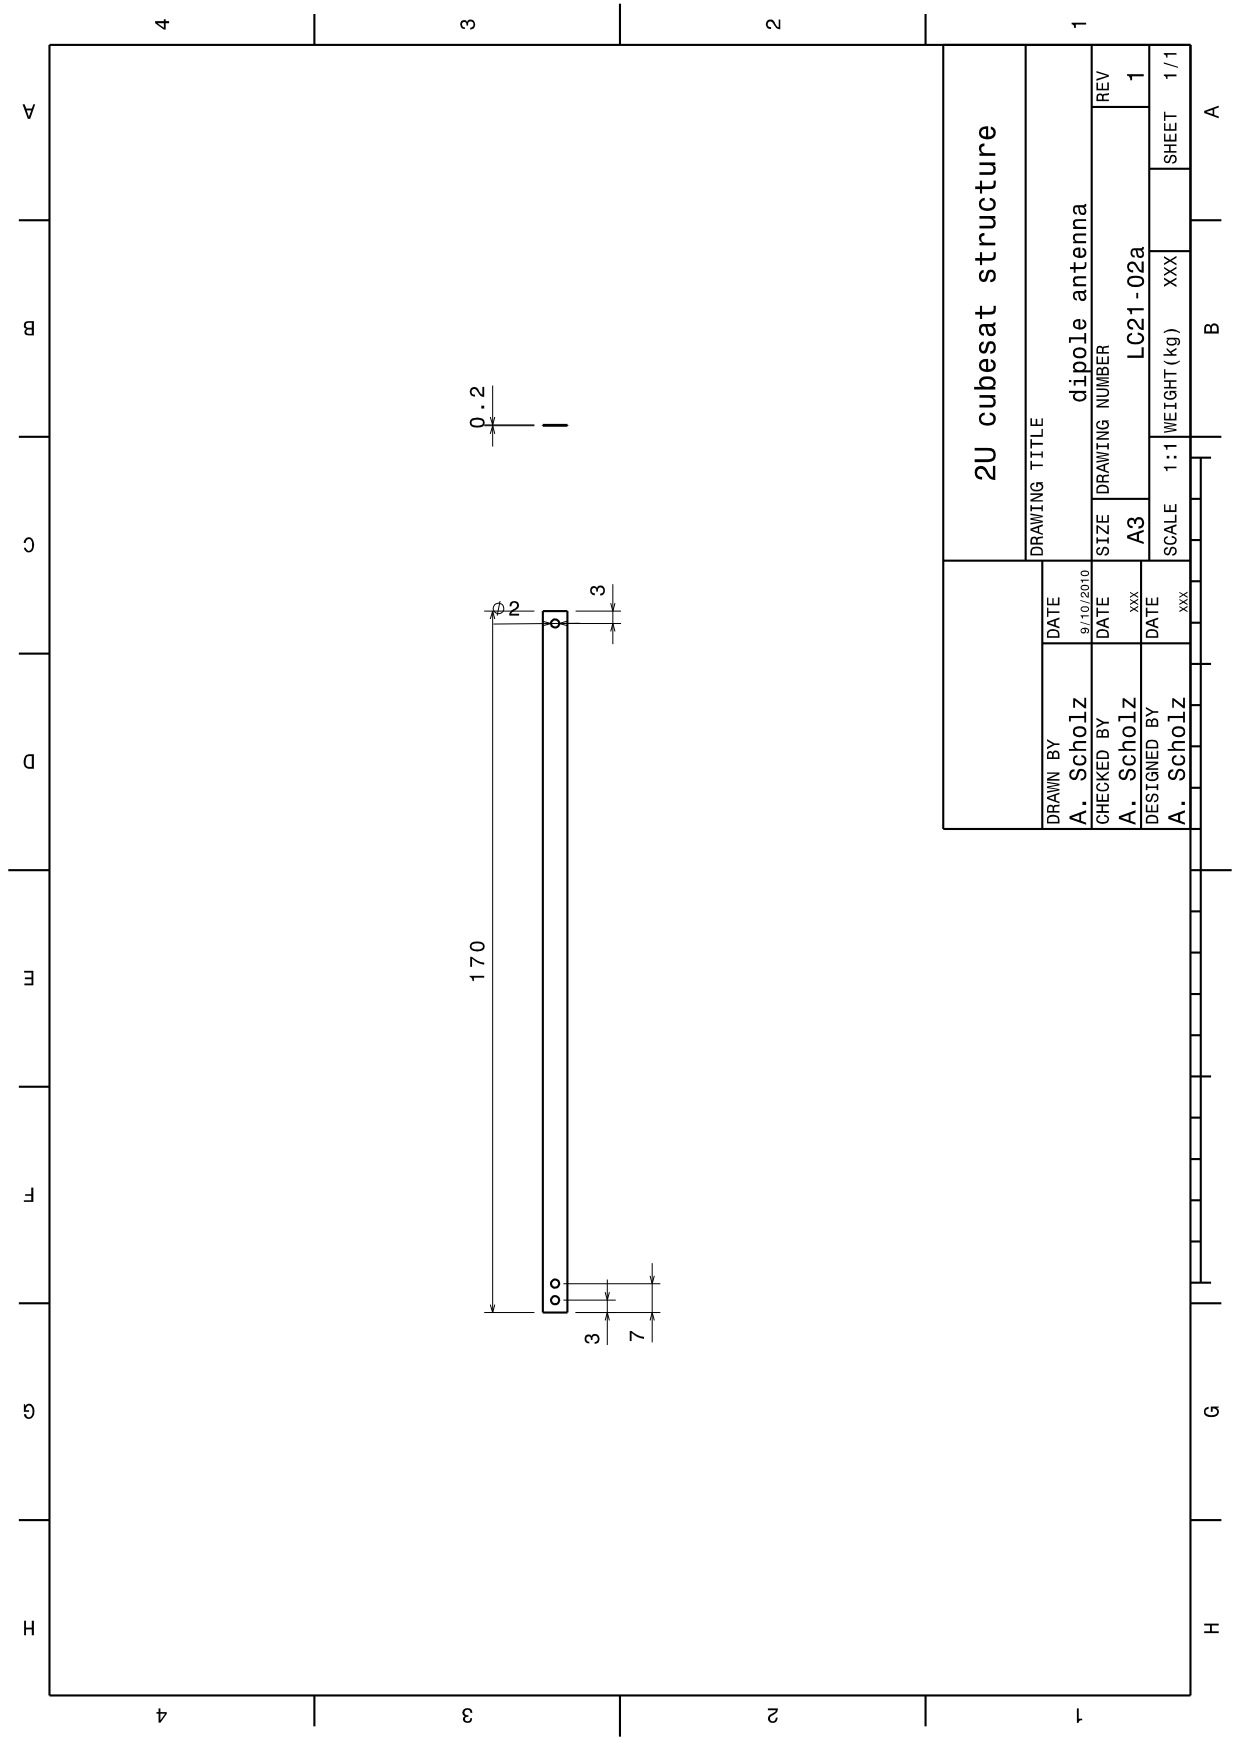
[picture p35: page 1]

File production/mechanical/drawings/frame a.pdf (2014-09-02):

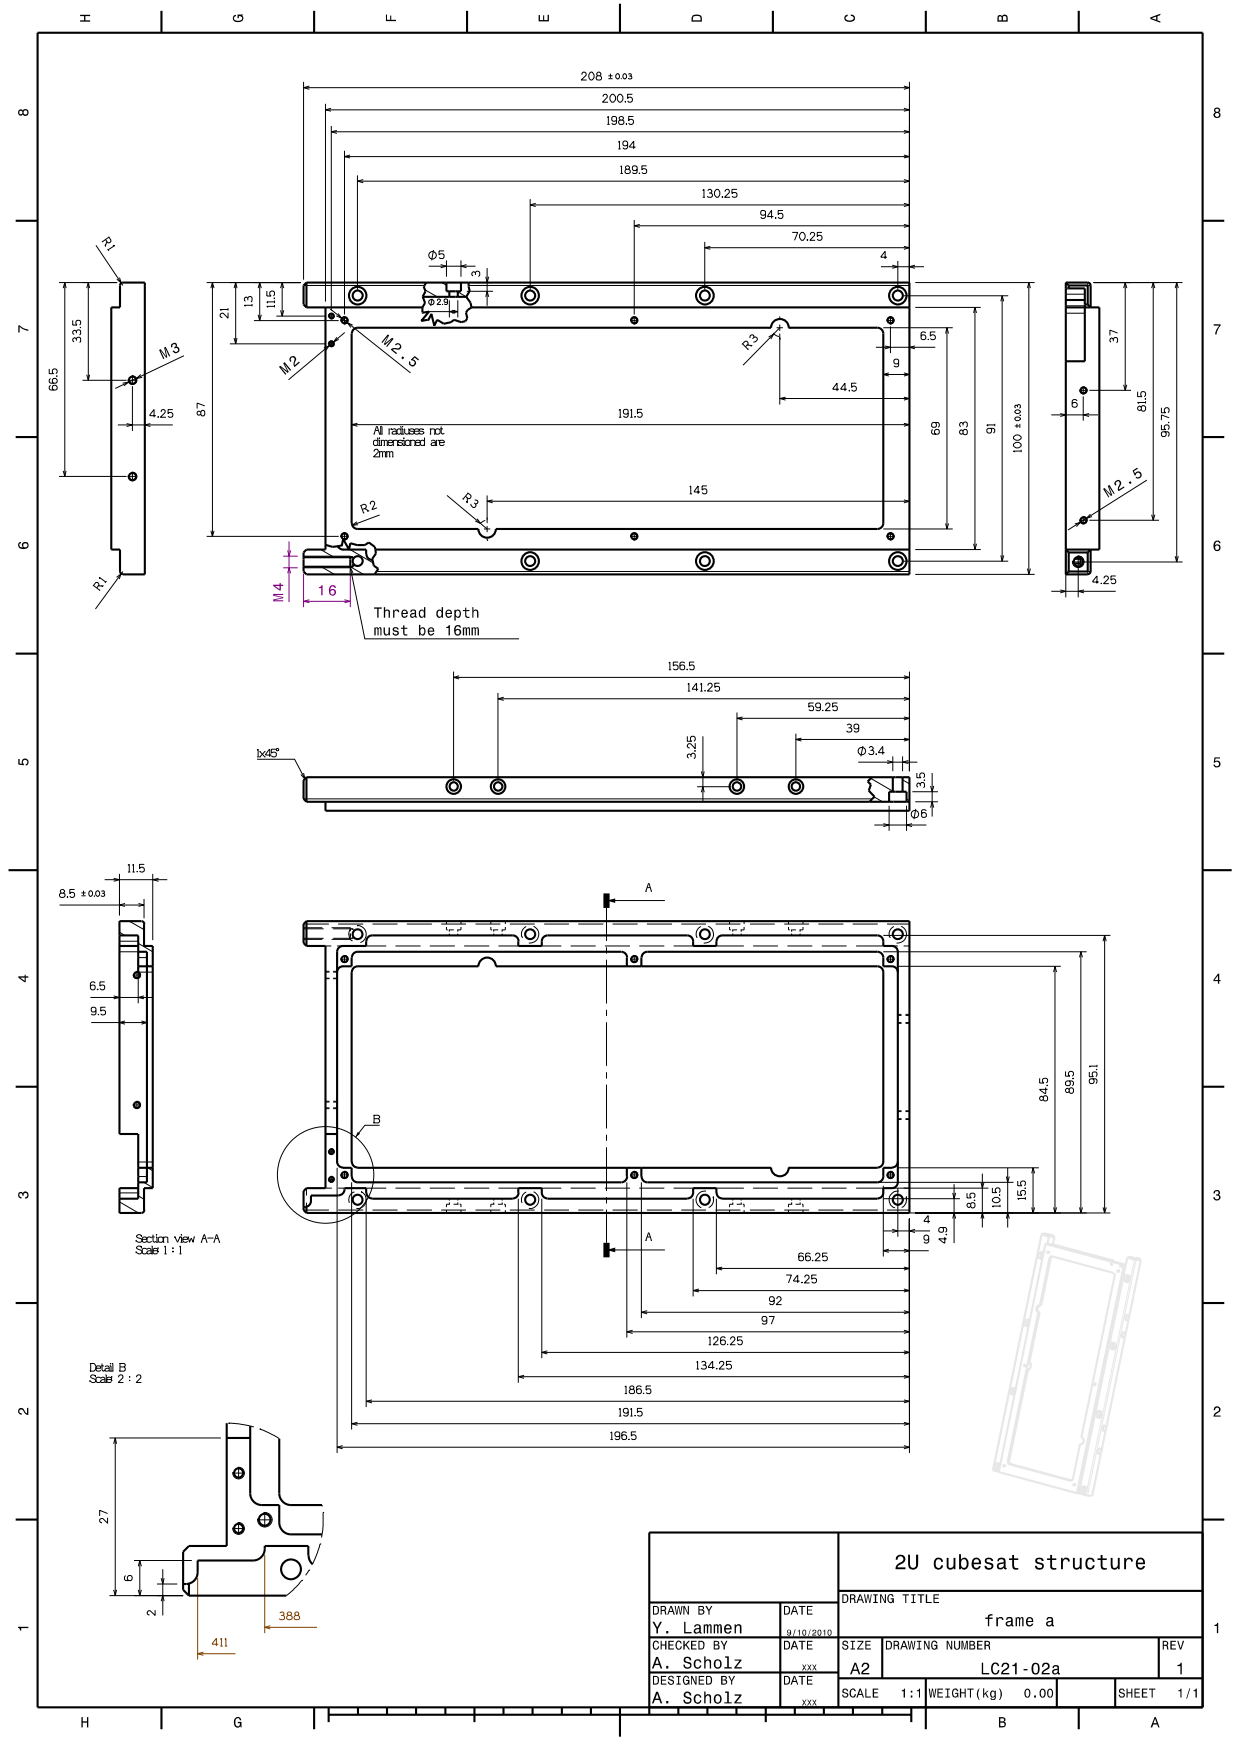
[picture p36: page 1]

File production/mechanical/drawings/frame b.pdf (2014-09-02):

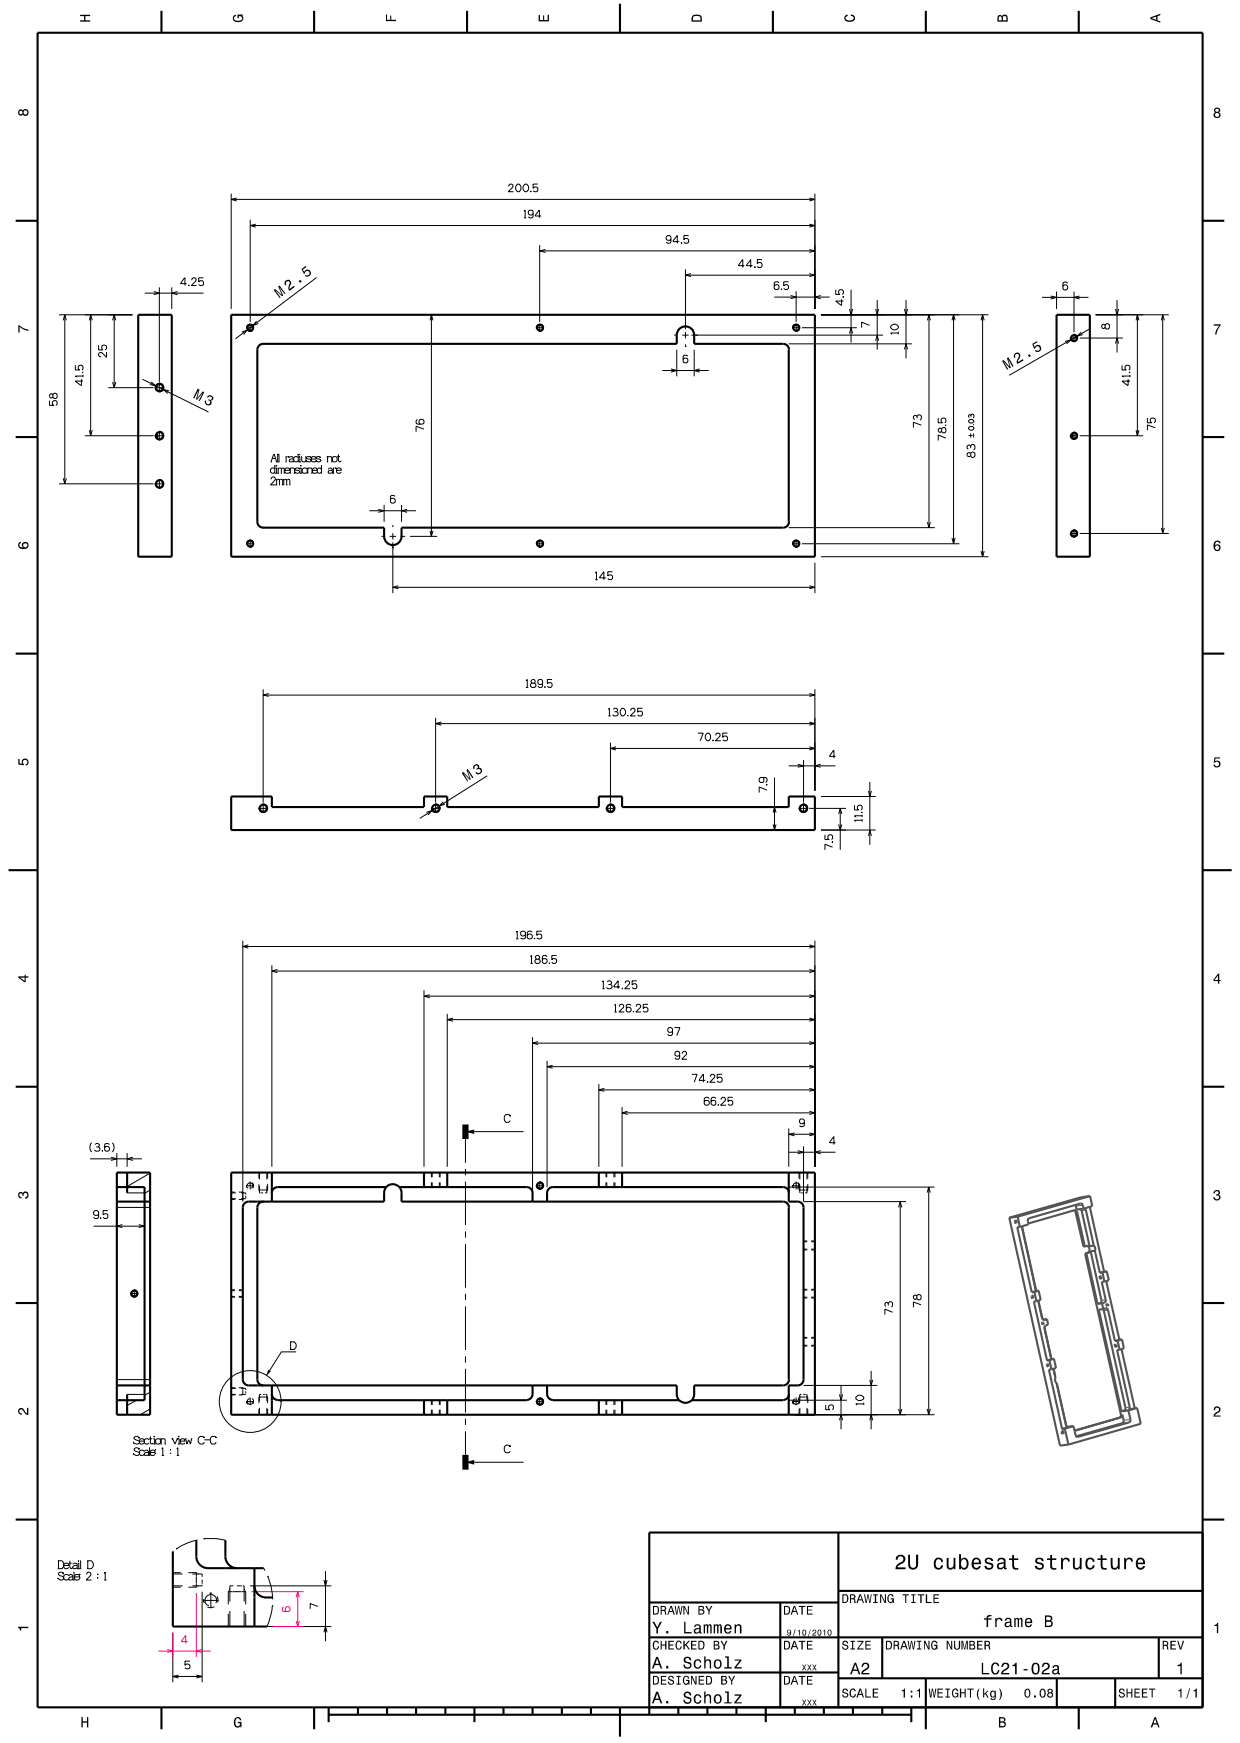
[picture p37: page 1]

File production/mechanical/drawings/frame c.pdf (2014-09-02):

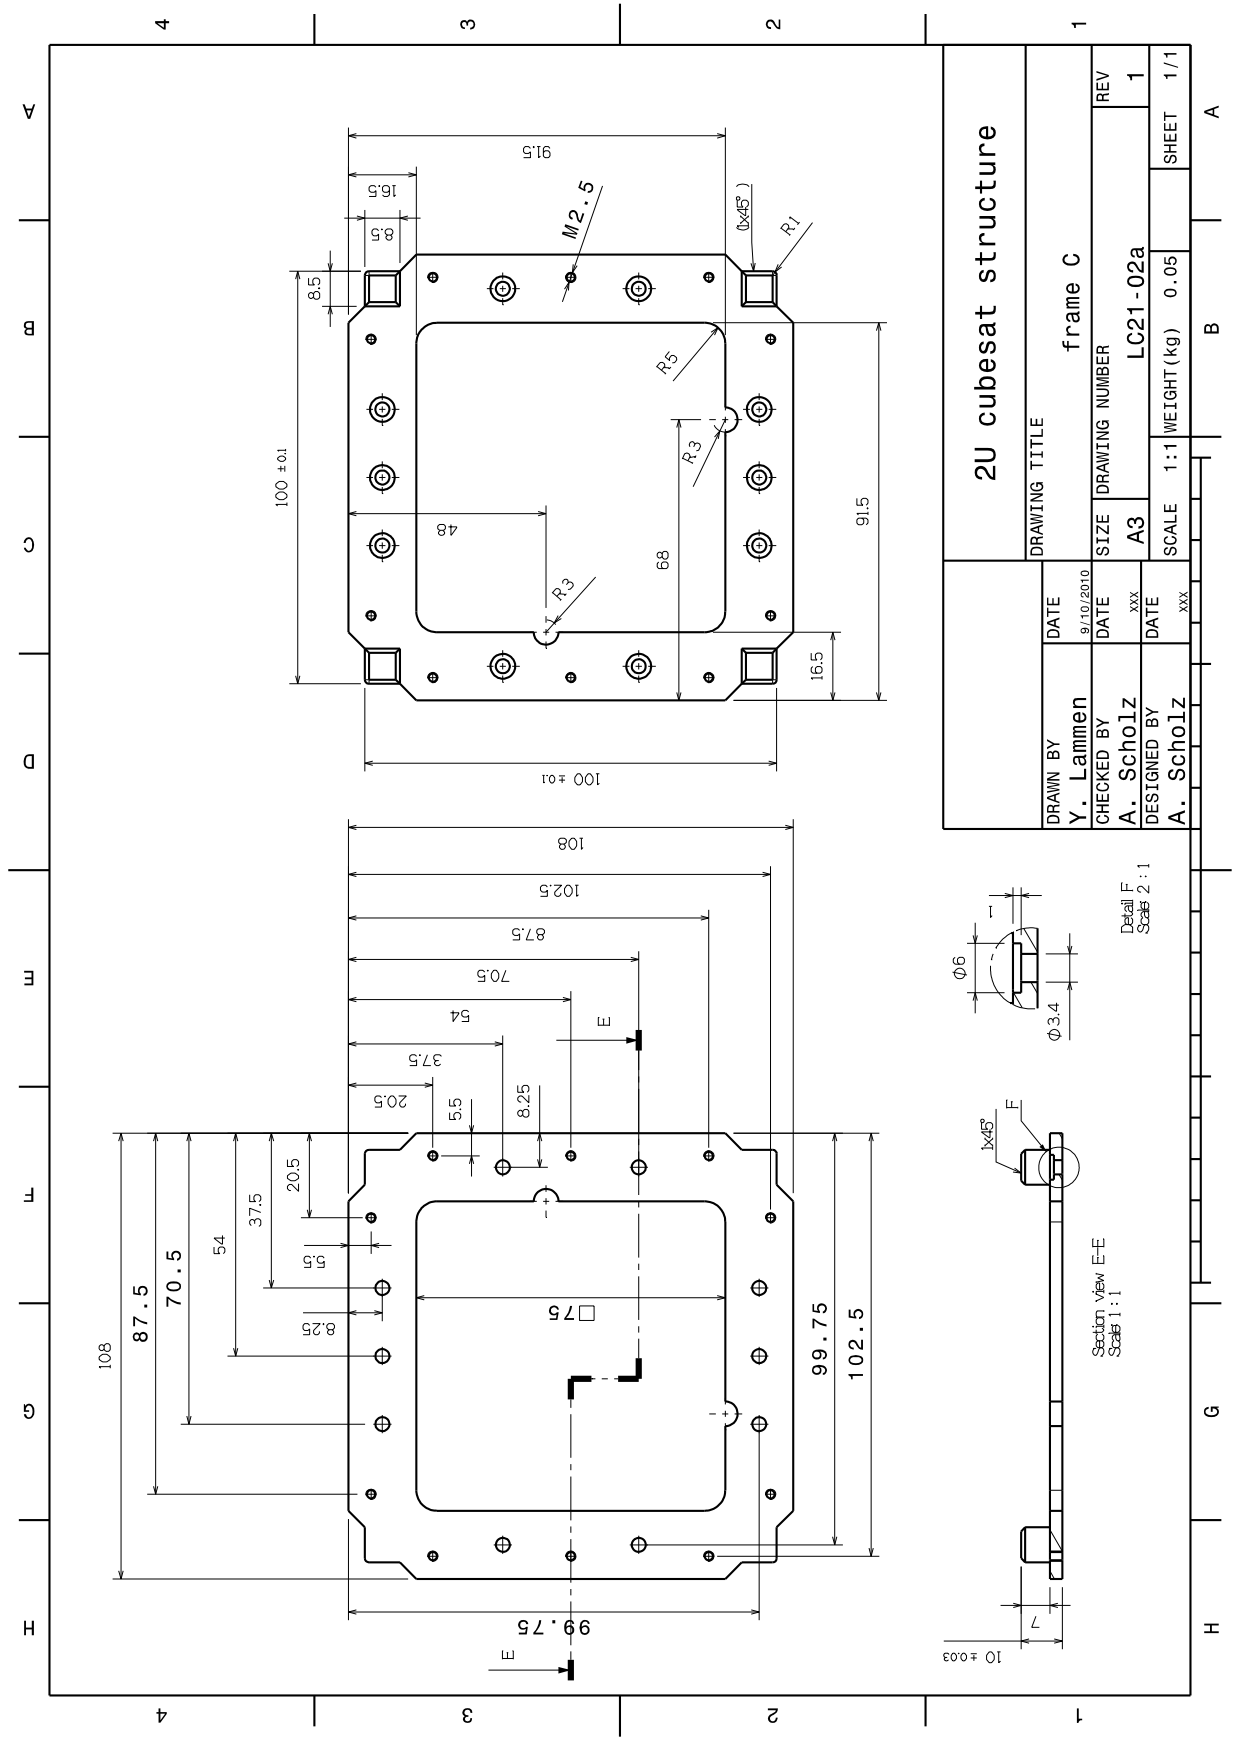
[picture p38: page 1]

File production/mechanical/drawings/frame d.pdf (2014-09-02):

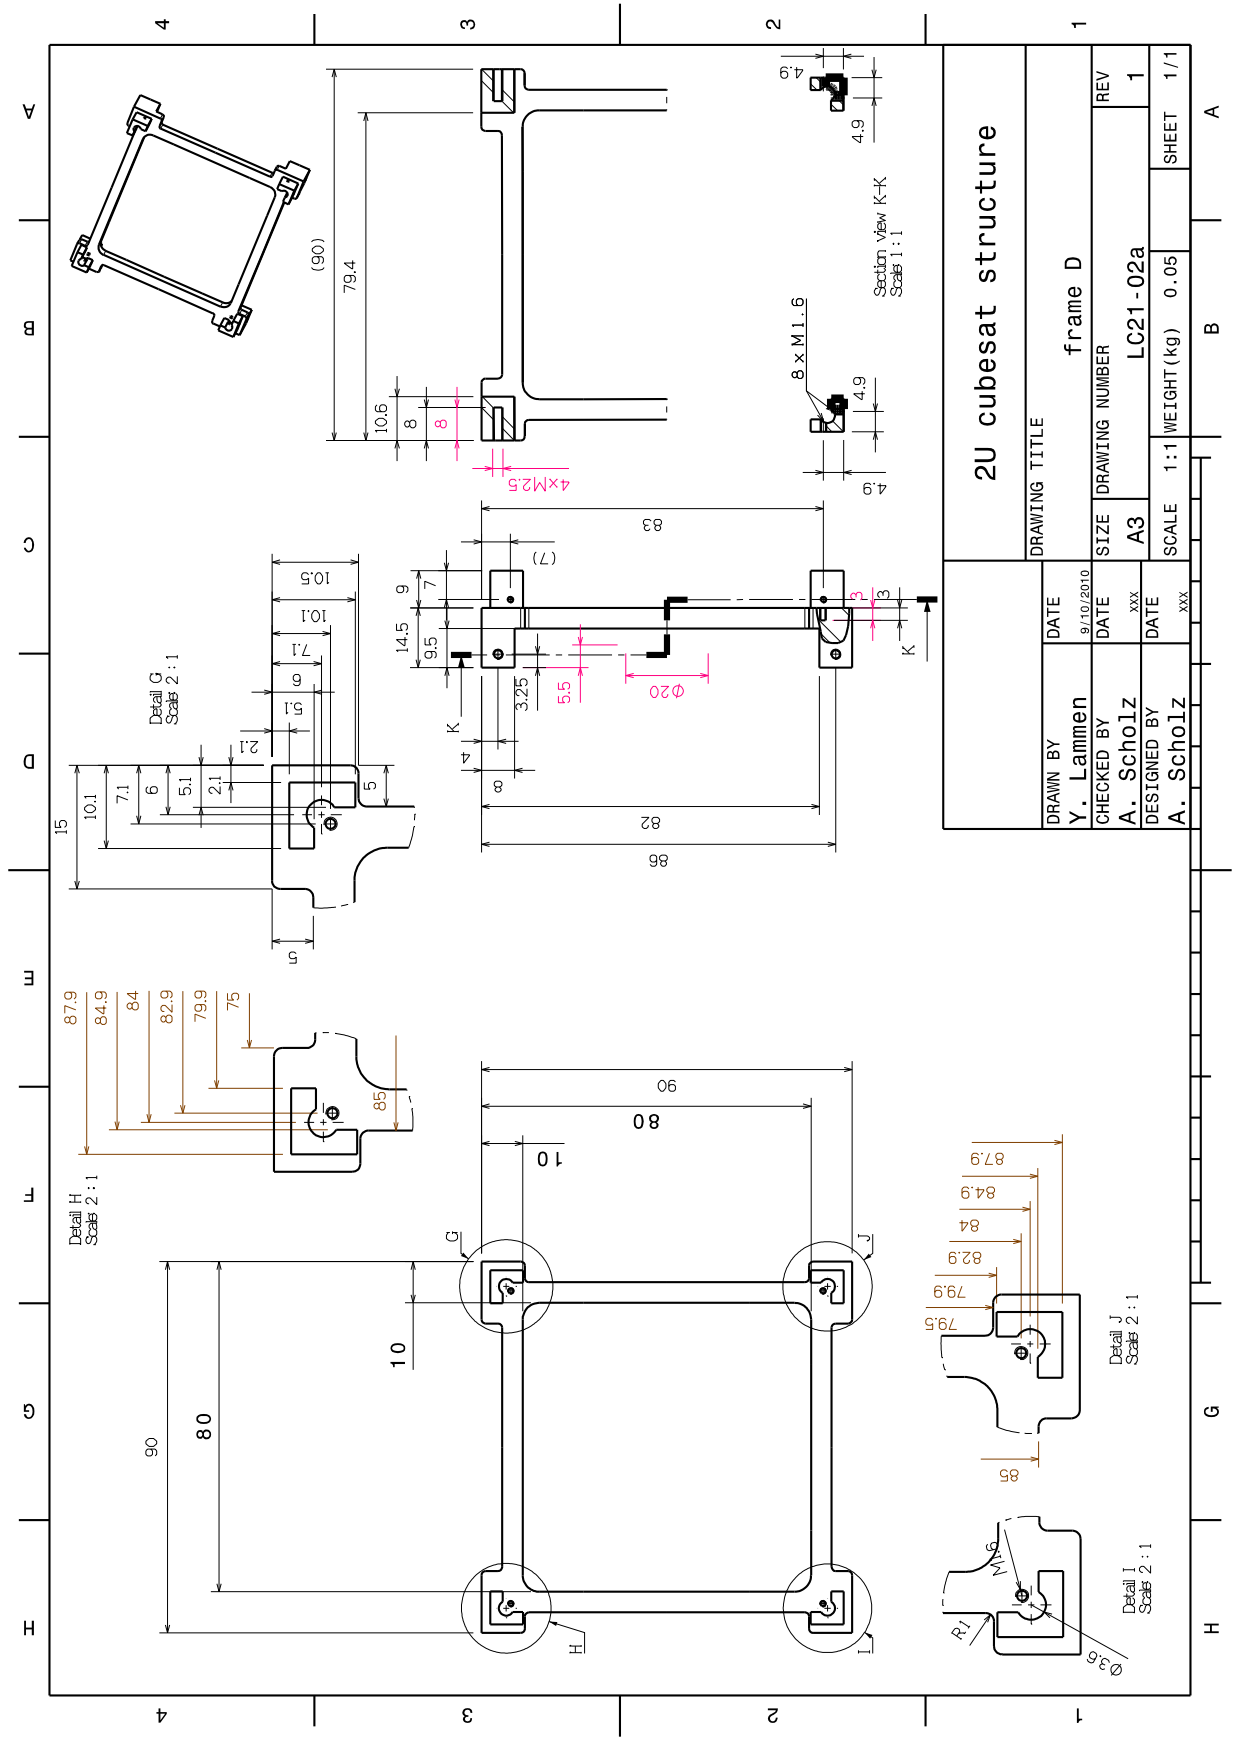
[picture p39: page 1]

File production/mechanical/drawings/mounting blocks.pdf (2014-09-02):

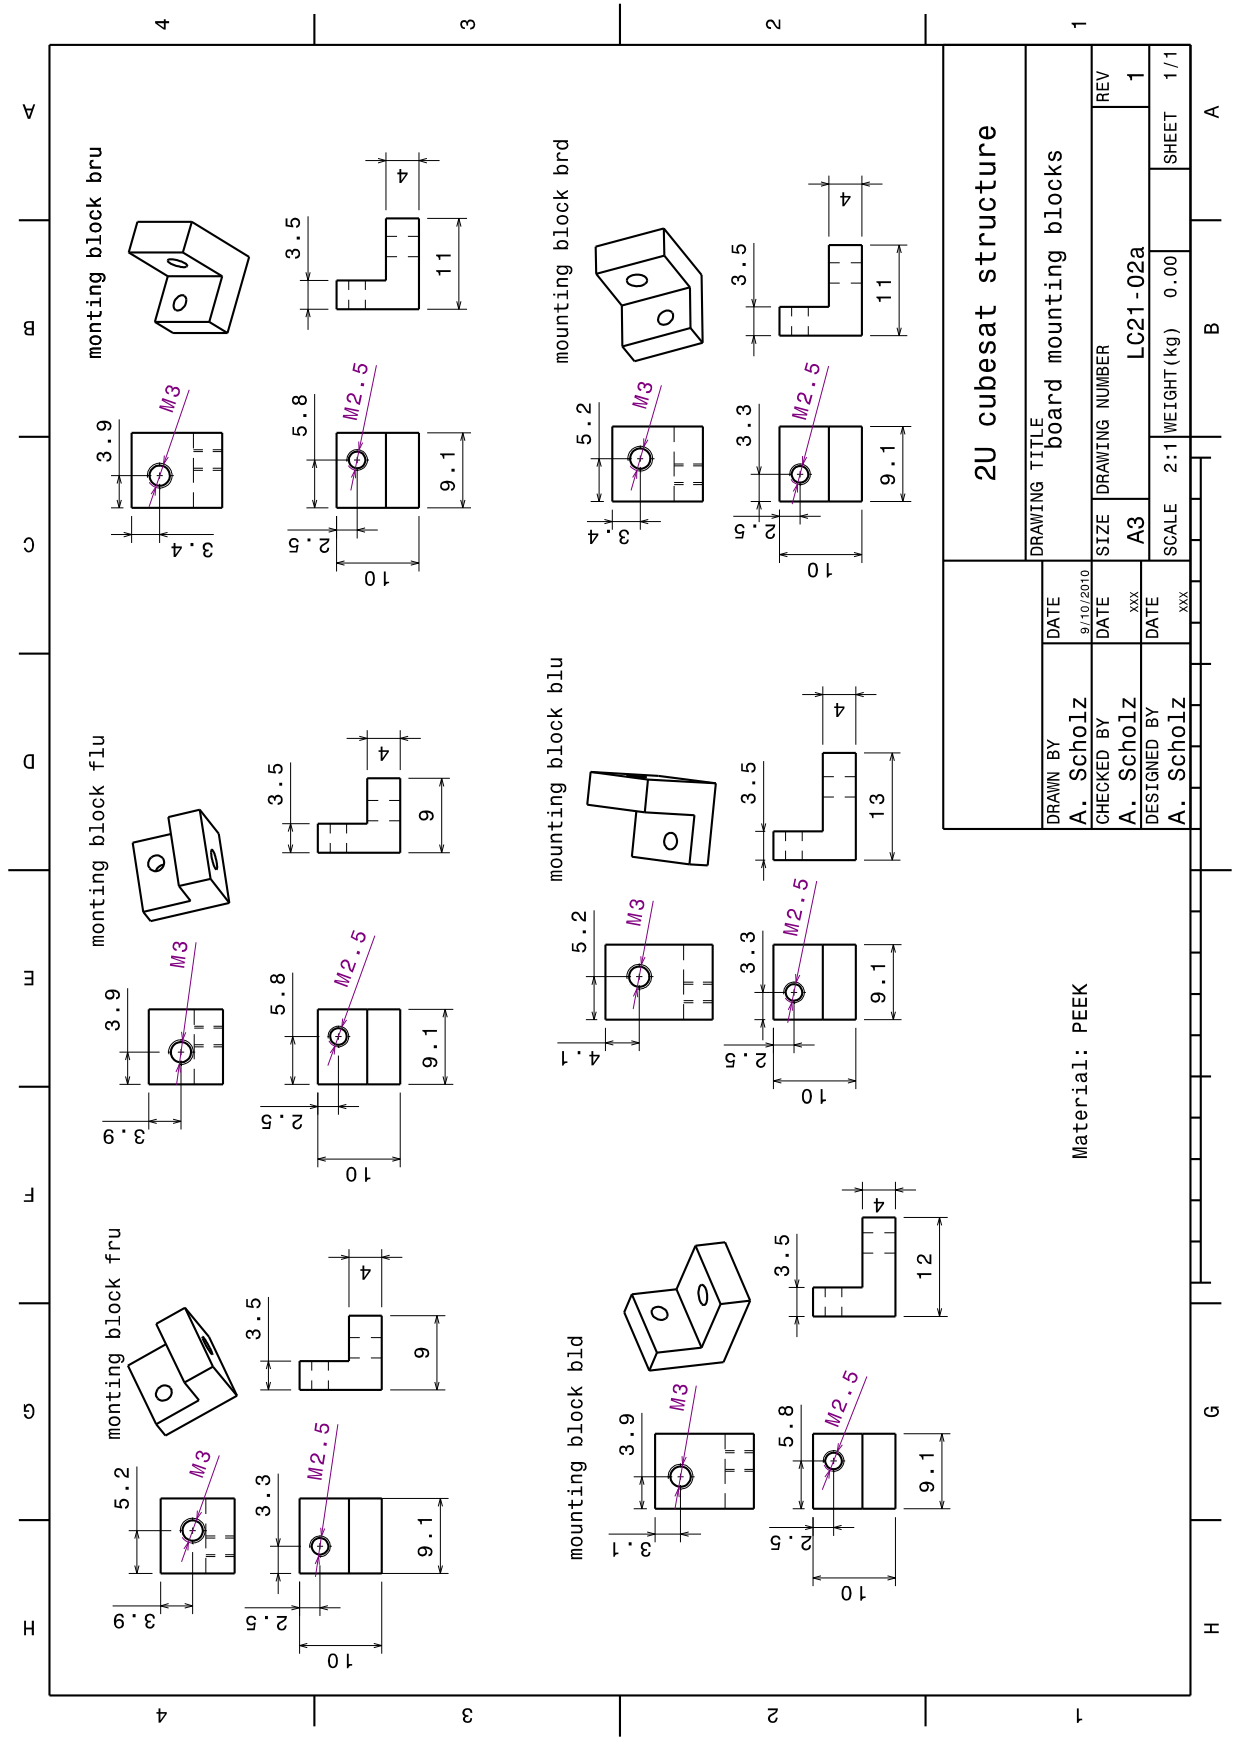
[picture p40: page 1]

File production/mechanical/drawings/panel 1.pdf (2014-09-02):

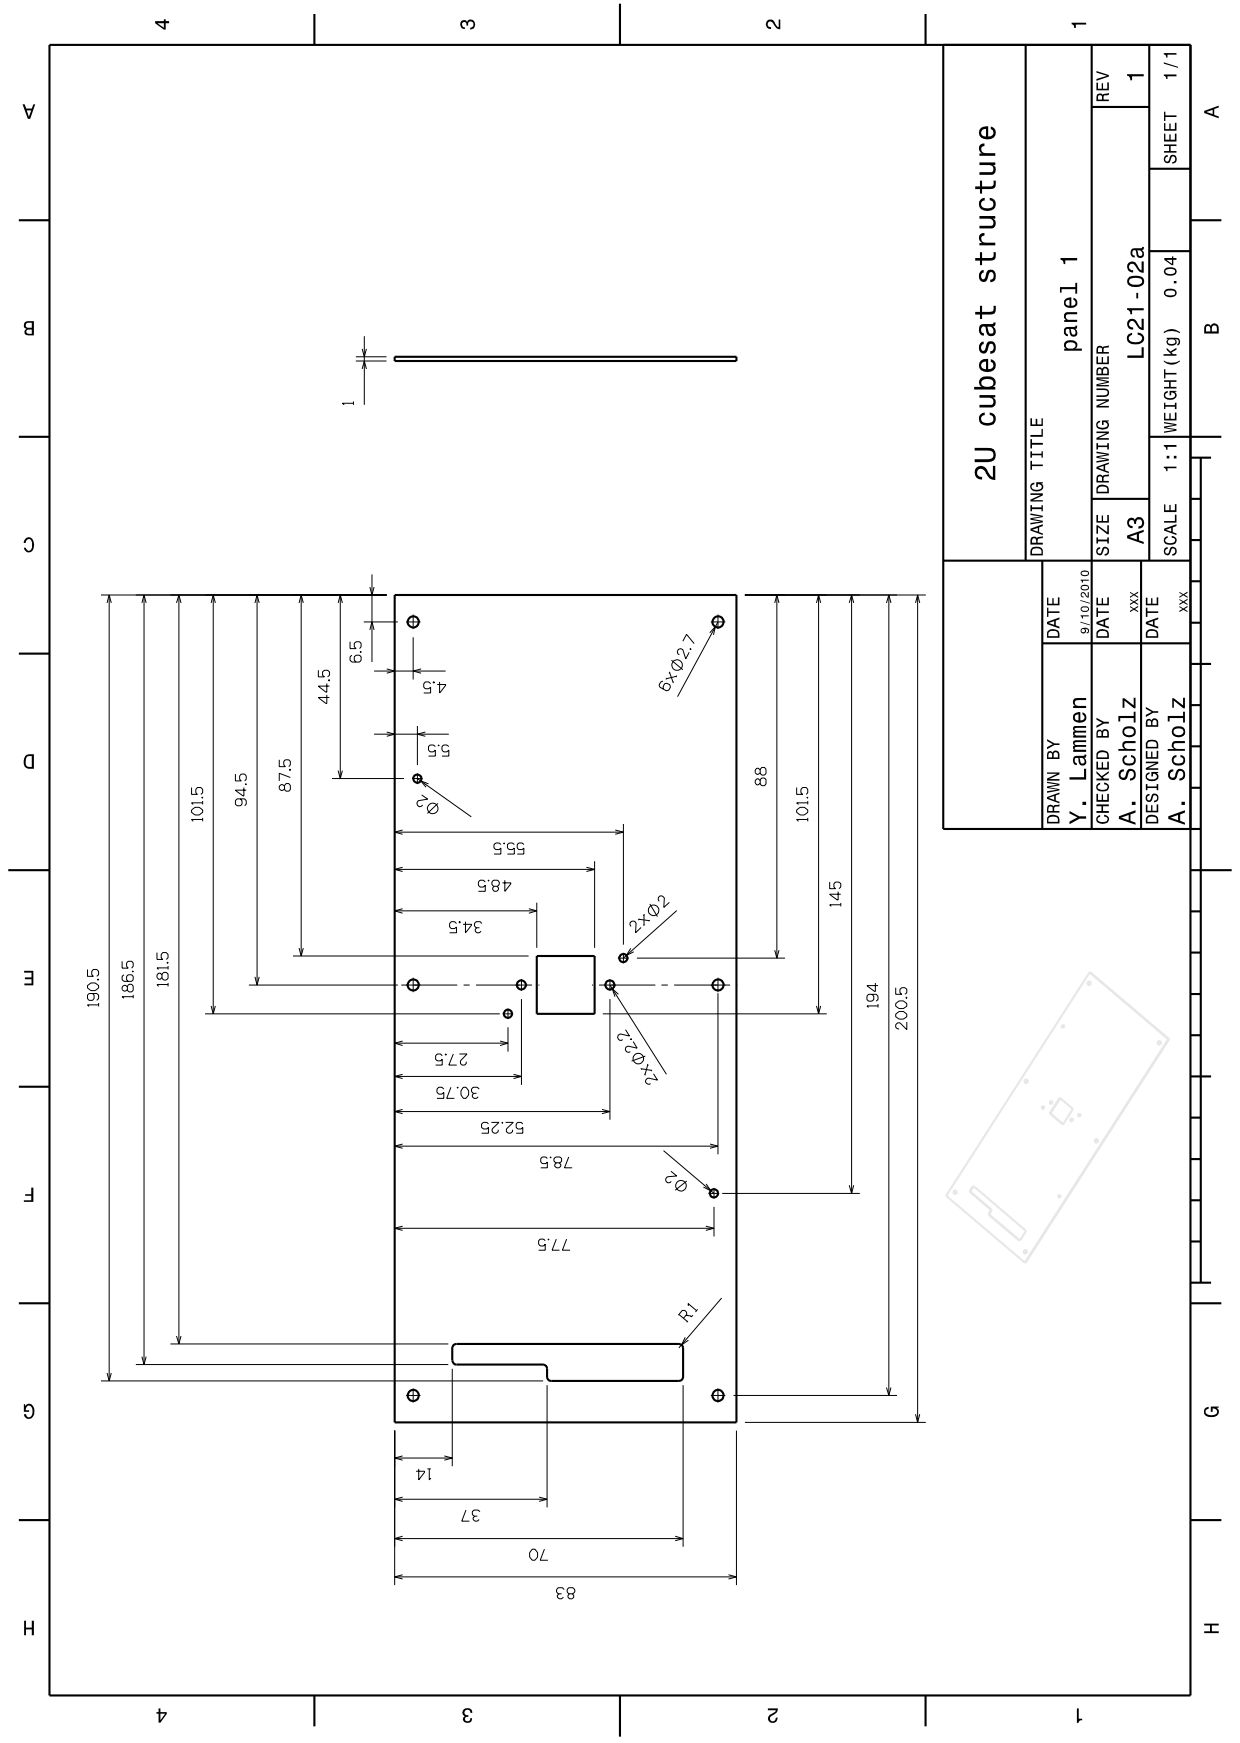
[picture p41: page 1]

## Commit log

2014-10-12 Removed PCB.
    [LC-2102a_bill_of_materials.ods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]
2014-10-25 Minor changes
    [LC-2102a bill of materials.ods]
2014-12-09 Move to own folder
    [LC-2102a bill of materials.ods]
